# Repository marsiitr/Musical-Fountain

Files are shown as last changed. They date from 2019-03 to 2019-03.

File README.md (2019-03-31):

 # Musical-Fountain

 

## Abstract

 The idea behind the project is that we use the concept of nodes in sound, and use it to control the movement of servos and the brightness of LEDs.  

 We also added a stepper motor which rotates the entire revolute at a constant 30 steps per second. We also added another stepper motor which would control a central valve.

The nozzles were 3d printed to reduce the mannufacturing cost. For insulation, we mostly used locally available epoxy glue and araldite. 

## Motivation

From the outside , musical fountain seemed to be a trivial project. but, when we got into its technical aspects, it wasn't so. Everytime we came up with a design, we had to brainstorm it and eventually a new design came into picture.   
This challenge of coming up with an efficient model is what kept us motivated.

## Electronic Aspect  

1. An app named Audacity was used to export the data points corresponding to a song(the value of the data points signifies the voltage values of the sound signals).The extracted data was analyzed and plotted to see the maximum and minimum value of the data points.In the arduino code, the stepper was given a rotation after every 10 iterations and servo were rotated as per a fixed pattern of iterations.  
2. The Leds were made to dance as per the data points value by giving the range of value between the maximum and minimum values calculated before.For every specific command, functions were made and were called when required in the void loop.Also one more stepper motor was attached to a flow regulator to regulate the flow of water coming to the central nozzle.  
3. Dataset was made for 5 songs.As the space available in the arduino is limited , we used sd card to store the data points value and read the corresponding value in the code directly from the sd card.Most of the electronic parts like motors and wires were in the water, hence all the components were completely sealed and water proofed so that no damage is caused by water.

## Mechanical Aspect  
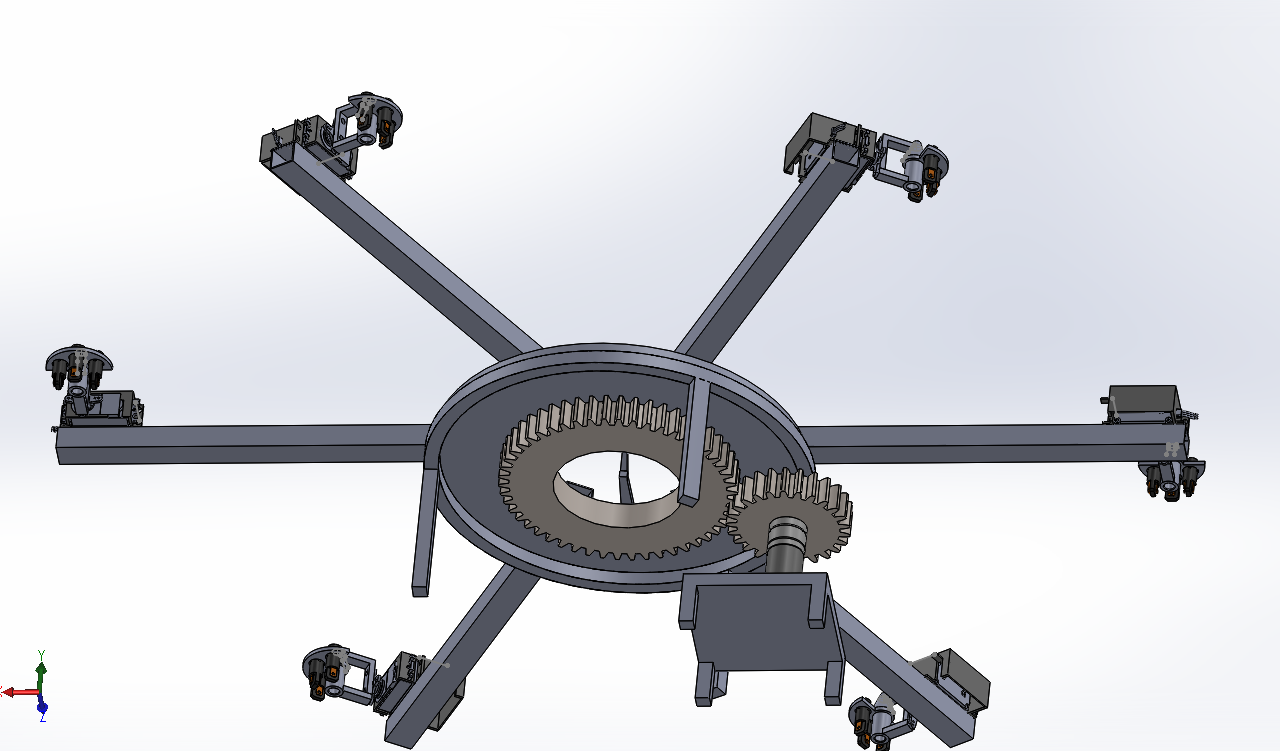
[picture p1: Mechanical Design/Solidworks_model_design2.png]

1. The revolute of the model was based on The Lazy Susan armature. we 3d printed the nozzles and 2 gears with 50 and 25 teeth respectively.  
2. 6 hollow tubes were attached on the lazy susan, at the end of each was a servo motor attached which would eventually control the movement of the nozzle.  
3. A secondary base was manufactured to setup the stepper motor which was used to rotate the armature. the secodary base also housed another stepper motor which would be controlling the valve. 3 pumps were used to pump water in the fountain.  

## Cost Structure  
|COMPONENTS | COST(₹)|
|----|---|
|Arduino Mega |  1300|
|Motor Drive |  160*2|
|Servo Motor |  325*6|
|Stepper | 690*2|
|Lazy Susan | 1250|
|Tub | 670|
|IC, BreadBoard, etc | 300|
|Wiring | 1000|
|LEDs | 350|
|M Seal, Araldite | 300|
|Aluminium Rod | 280|
|Central Valve | 300|
|Pump | 2000|
|Piping | 700 |
|Total Estimated Cost | 11,500|

## Application  

It has been observed that when soothing music is played near crops, there yeild increases. So this technique will be very helpful in drip irrigation. 
Also, musical fountain increases the aesthetic value of the place where it is established.  

## Limitation  

Our fountain's performance was greatly hindered by the pumps we used. Low quality piping and insulation can also be a contributing factor for bad performance.  
## Future Improvements  

We can improve the quality and way of insulation which was provided to the fountain's electrical components. Its base needed attention too. Also, pumps with higher values of Q should be used.  

## Team Members  

1. Archi Agarwal
2. Jalaj Madaan
3. Kshitij Srikant
4. Tabish Madni
5. Tejas Naik
6. Vaibhavi Chidella
7. Vipul Bansal  

## Mentors

1. Prachi Agarwal
2. Vandan Gajjar

## References  

1. https://ieeexplore.ieee.org/abstract/document/5230466
2. https://manual.audacityteam.org/man/tutorials.html
3. https://www.arduino.cc/en/Reference/SD
4. https://matplotlib.org/tutorials/introductory/pyplot.html
5. And some of the tips and ideas given by seniors :)

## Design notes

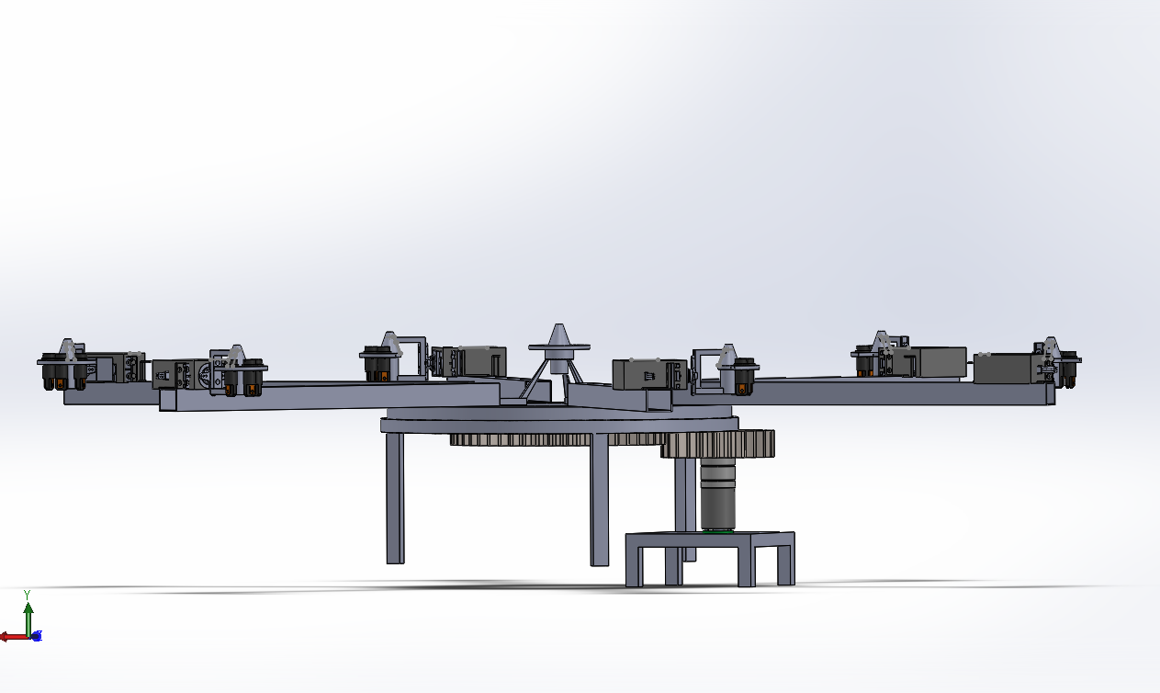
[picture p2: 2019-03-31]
Mechanical Design/Solidworks_model_design1.png

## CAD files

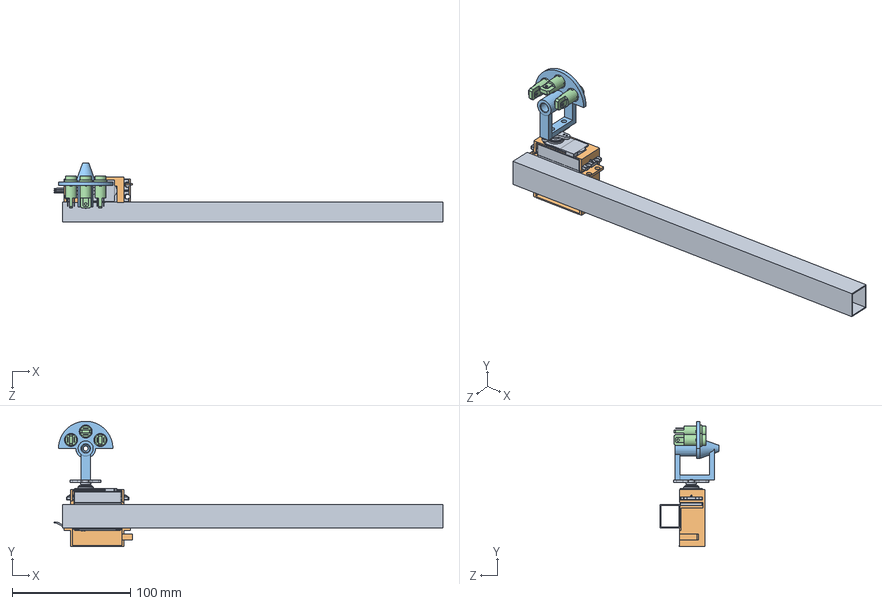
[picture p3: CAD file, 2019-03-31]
Mechanical Design/rod nossel.SLDASM
328.6 x 106.0 x 50.2 mm
rod
cover
sample 10
led x 3

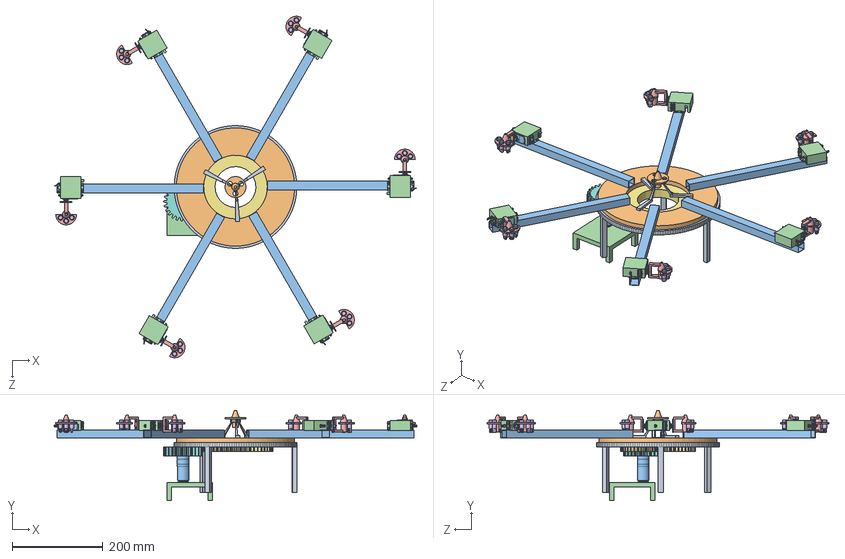
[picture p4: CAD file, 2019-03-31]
Mechanical Design/new musical fountain assembly.SLDASM
798.1 x 198.3 x 751.1 mm
lazy susan base
lazy susan representation
rod x 6
cover x 6
sample 10 x 6
led x 18
1 Inch - Spur gear 8DP 50T 14.5PA 0.787401575FW ---S50N3.0H2.0L0.03125N
Inch - Spur gear 8DP 25T 14.5PA 0.787401575FW ---S25N3.0H2.0L0.03125N
centre nossel base
centre nossel
Pololu-25D-12V-21kgcm-DCmotor
encoder base

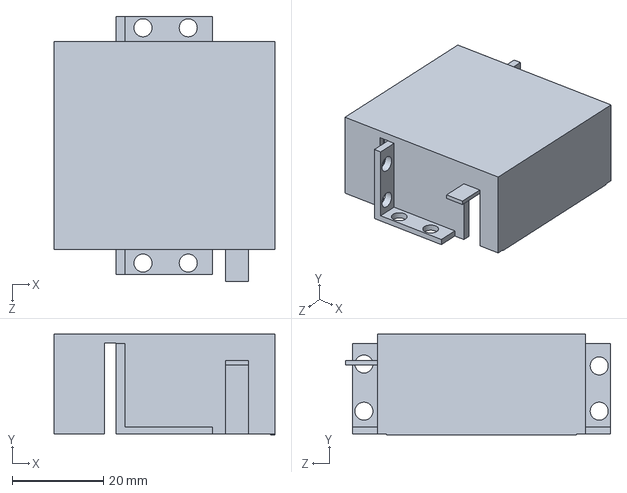
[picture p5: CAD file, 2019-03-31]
Mechanical Design/cover.SLDPRT
48.3 x 22.0 x 57.9 mm

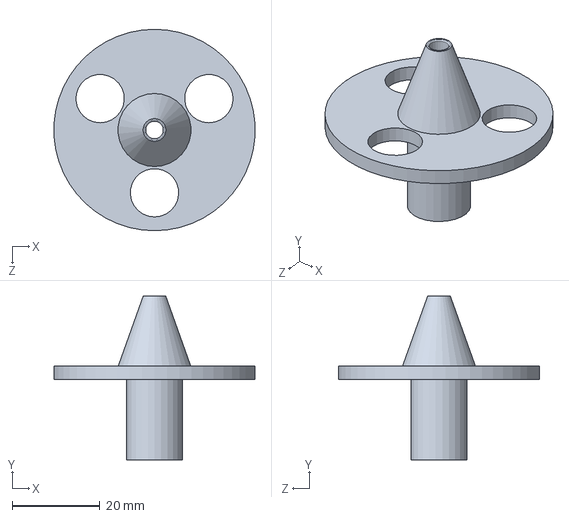
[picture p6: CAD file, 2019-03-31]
Mechanical Design/centre nossel.SLDPRT
45.9 x 37.4 x 46.0 mm

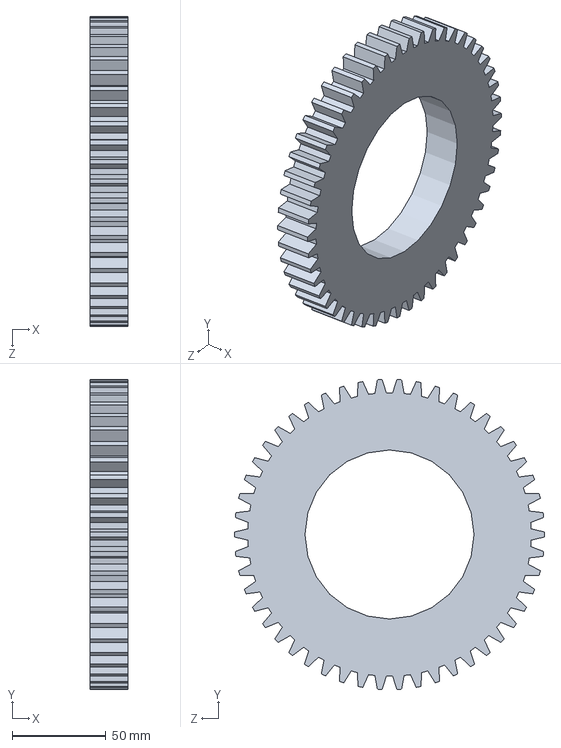
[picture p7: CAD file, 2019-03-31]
Mechanical Design/Gear Inch - Spur gear 8DP 50T 14.5PA 0.787401575FW ---S50N3.0H2.0L0.03125N.SLDPRT
20.0 x 164.9 x 165.1 mm

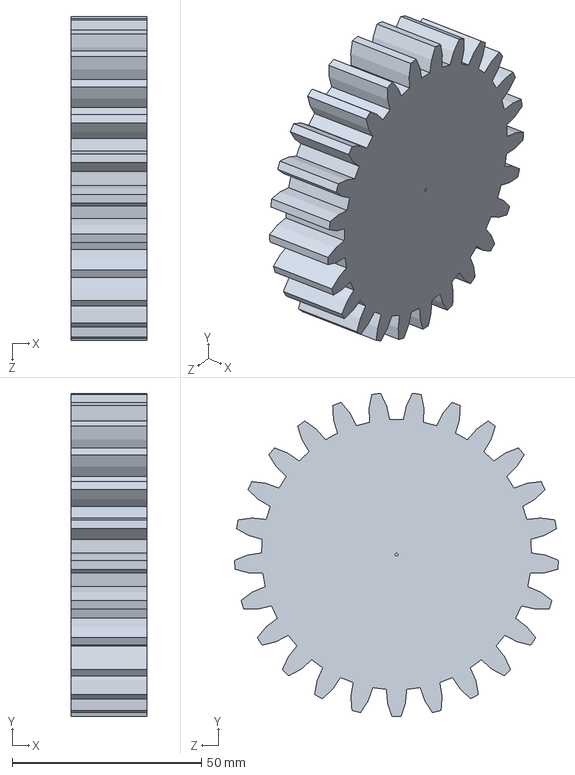
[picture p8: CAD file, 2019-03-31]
Mechanical Design/Inch - Spur gear 8DP 25T 14.5PA 0.787401575FW ---S25N3.0H2.0L0.03125N.sldprt
20.0 x 85.5 x 85.7 mm

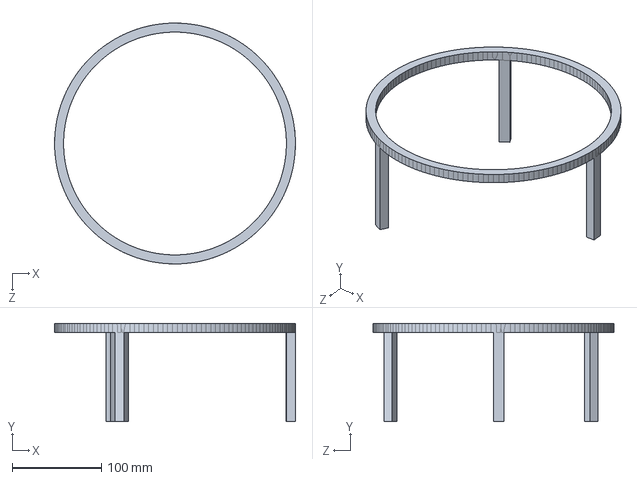
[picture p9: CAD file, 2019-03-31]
Mechanical Design/lazy susan base.SLDPRT
270.0 x 110.0 x 270.0 mm

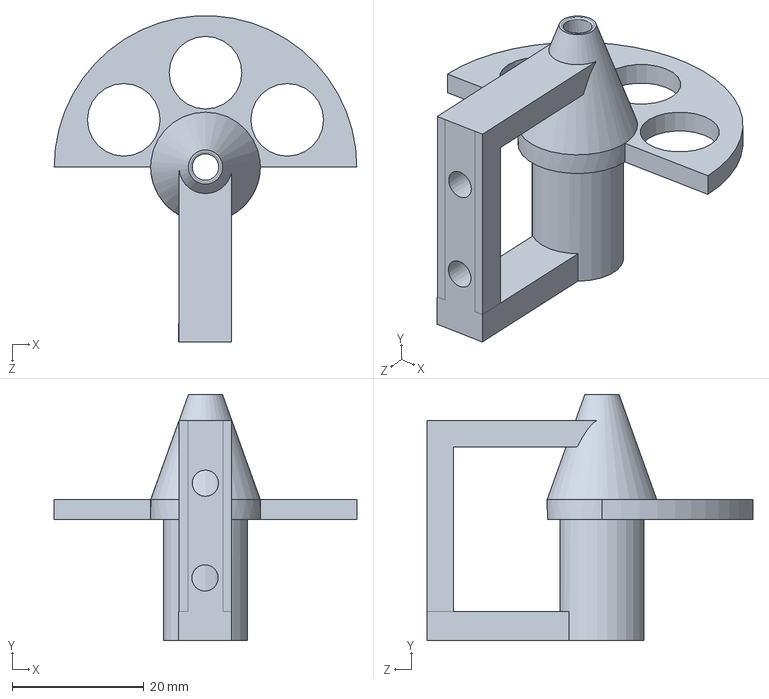
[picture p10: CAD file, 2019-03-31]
Mechanical Design/side nossel.SLDPRT
46.0 x 37.4 x 49.5 mm

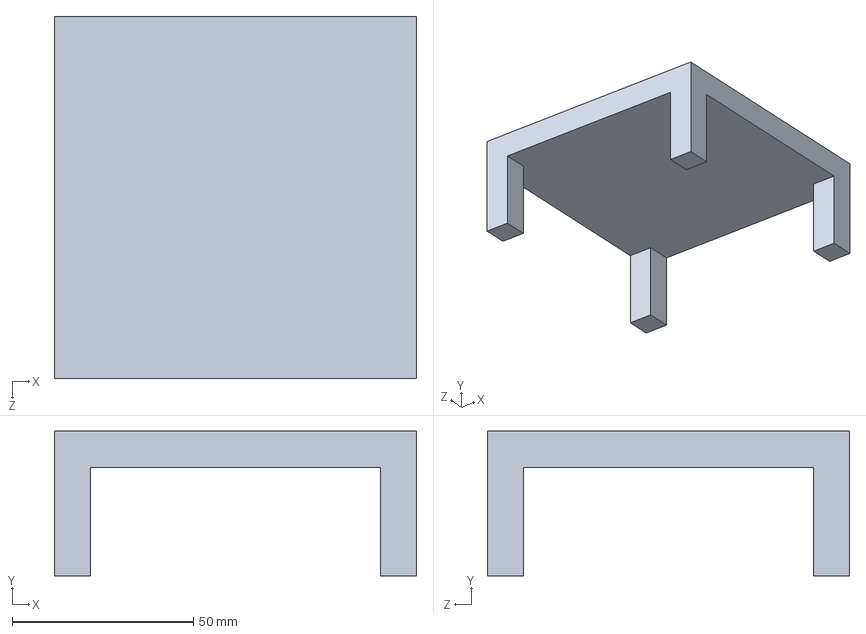
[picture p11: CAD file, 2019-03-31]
Mechanical Design/encoder base.SLDPRT
100.0 x 40.0 x 100.0 mm

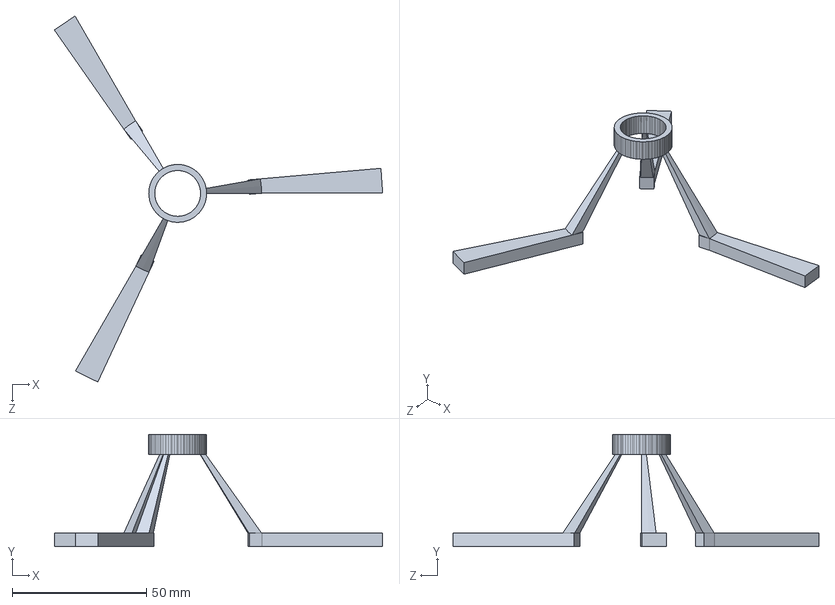
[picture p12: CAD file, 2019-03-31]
Mechanical Design/centre nossel base.SLDPRT
122.3 x 41.7 x 136.4 mm

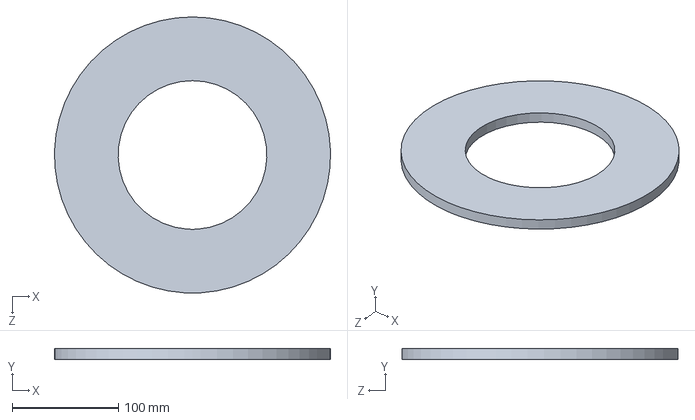
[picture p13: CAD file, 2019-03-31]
Mechanical Design/lazy susan representation.SLDPRT
259.9 x 10.0 x 260.0 mm

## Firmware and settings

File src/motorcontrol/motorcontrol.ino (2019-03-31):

#define s1 7           //defining servo pins on arduino
#define s2 8
#define s3 9
#define s4 10
#define s5 11
#define s6 12
#include <Servo.h>        //including servo library
#include <Stepper.h>      //including stepper library
int i =0;
int a1=200;            
int a2=20;

 int stepsPerRevolution = 200;                         // defining steps per Revolution for the stepper
Stepper myStepper(stepsPerRevolution, A0,A1,A2,A3);    //setting the stepper for gear revolution
Stepper myStepper1(stepsPerRevolution, 2,3,4,5);       //setting the stepper1 for controlling the flow regulator
Servo myservo1;                           //setting the servos                                                                                          
Servo myservo2;
Servo myservo3;
Servo myservo4;
Servo myservo5;
Servo myservo6;
void servoset()                 //function for setting the servo to 0 position

{myservo1.write(0);
myservo2.write(0);
myservo3.write(0);
myservo4.write(0);
myservo5.write(0);
myservo6.write(0);
  
}
void servomove(double x)         //function for the motion of servo to any angle x
{myservo1.write(x);
myservo2.write(x);
myservo3.write(x);
myservo4.write(x);
myservo5.write(x);
myservo6.write(x);
  
}
void motion() {                      //function for the motion of stepper
  // step one revolution  in one direction:
  Serial.println("clockwise");
  myStepper.step(a1);
a1=-a1;             //for making it revolve the other way
}
void motion2() {                    //function for the motion of stepper1
  myStepper1.step(a2);
  a2=-a2;
}
void setup() {
  // put your setup code here, to run once:
  Serial.begin(9600);

  myservo1.attach(s1);             //initializing the servos
myservo2.attach(s2);
myservo3.attach(s3);
myservo4.attach(s4);
myservo5.attach(s5);
myservo6.attach(s6);
 myStepper.setSpeed(30);          //setting the stepper speed
 myStepper1.setSpeed(10);         //setting the stepper1 speed

}

void loop() {
  // put your main code here, to run repeatedly:
  
  for (i=1;i<=9856;i++){                         //iterating over the number of data points obtained

  if(i%5==0 && i%30!=0 && i%20!=0 && i%10!=0)
 {
  servomove(25);
 }
 if (i%10==0 && i%30!=0 && i%20!=0){
servomove(0);
}
 if(i%20==0 && i%30!=0)
 {
  //motion();
  servomove(25);
  motion2();
  
 }
 if(i%30==0){
  servomove(0);
  motion();
  }
  }
 
  

}

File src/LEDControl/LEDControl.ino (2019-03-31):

#define oi 2        //defining pin for centre nozzle orange colour led
#define wi 3         //defining pin for centre nozzle white colour led
#define ri 5          //defining pin for centre nozzle red colour led
#define go 6           //defining pin for outer nozzles green colour led
#define wo 7            //defining pin for outer nozzles white colour led
#define ro 8             //defining pin for outer nozzles red colour led


#include <Servo.h>       //including servo library
#include <SD.h>          //including library for read from an sd card connected to arduino
#include <SPI.h>         //including library for connecting sd card to arduino
#include <Stepper.h>     //including stepper library
File myFile;

float readLineUser()
{
  String r;
  char c;
  while(myFile.available())
  {
    c=myFile.read();
    if(c==',')
    {
      return (r.toFloat());
    }
    else if(c=='\n')
    {
      r="";
      
    }
    else
    {
      r+=c;
    }
  }
}

//below are the functions for glowing and turning off different leds in pairs
void ored()
{
  digitalWrite(oi,HIGH);
  digitalWrite(ro,HIGH);
}
void ogreen()
{
  digitalWrite(oi,HIGH);
  digitalWrite(go,HIGH);
}
void owhite()
{
  digitalWrite(oi,HIGH);
  digitalWrite(wo,HIGH);
}
void wred()
{
  digitalWrite(wi,HIGH);
  digitalWrite(ro,HIGH);
}
void wgreen()
{
  digitalWrite(wi,HIGH);
  digitalWrite(go,HIGH);
}
void rgreen()
{
  digitalWrite(ri,HIGH);
  digitalWrite(go,HIGH);
}
void rwhite()
{
  digitalWrite(ri,HIGH);
  digitalWrite(wo,HIGH);
}
void multi()
{
  digitalWrite(oi,HIGH);
  digitalWrite(wi,HIGH);
  digitalWrite(ri,HIGH);
  digitalWrite(wo,HIGH);
  digitalWrite(ro,HIGH);
  digitalWrite(go,HIGH);
}
void low()
{
  digitalWrite(oi,LOW);
  digitalWrite(wi,LOW);
  digitalWrite(ri,LOW);
  digitalWrite(wo,LOW);
  digitalWrite(ro,LOW);
  digitalWrite(go,LOW);
}


void setup() {

 
  
pinMode(oi,OUTPUT);
pinMode(wi,OUTPUT);
pinMode(ri,OUTPUT);
pinMode(go,OUTPUT);
pinMode(wo,OUTPUT);
pinMode(ro,OUTPUT);
 // Open serial communications and wait for port to open:
  Serial.begin(9600);
  while (!Serial) {
    ; // wait for serial port to connect. Needed for native USB port only
  }


  Serial.print("Initializing SD card...");

  if (!SD.begin(4)) {
    Serial.println("initialization failed!");
    while (1);
  }
  Serial.println("initialization done.");
 myFile = SD.open("SongData.txt");
  // open the file. note that only one file can be open at a time,
  // so you have to close this one before opening another.
}
void loop() {
   myFile = SD.open("SongData.txt");
  while(myFile.available()) {
    double s=readLineUser();                     //storing the data point value in a variable s
    low();
    
if ((s>0)&&(s<=5)){
 multi();
 }
 if ((s>5)&&(s<=10)){
  ored();
 }
if ((s>10)&&(s<=15)){
  ogreen();
 }  
if ((s>15)&&(s<=20)){
  owhite();
 }
if ((s>920)&&(s<=25)){
wred();
 }
 if ((s>25)&&(s<=30)){
 wgreen();
 }
 if ((s>30)&&(s<=35)){
  rgreen();
 }
 if ((s>35)){
 rwhite();
 }
 

 delay(107.54);
 
}
  
myFile.close();
}

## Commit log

2019-03-31 changes done
    [Gear Inch - Spur gear 8DP 50T 14.5PA 0.787401575FW ---S50N3.0H2.0L0.03125N.SLDPRT, Inch - Spur gear 8DP 25T 14.5PA 0.787401575FW ---S25N3.0H2.0L0.03125N.sldprt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]
2019-03-31 Created new folder A
    [Gear Inch - Spur gear 8DP 50T 14.5PA 0.787401575FW ---S50N3.0H2.0L0.03125N.SLDPRT, Inch - Spur gear 8DP 25T 14.5PA 0.787401575FW ---S25N3.0H2.0L0.03125N.sldprt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]
2019-03-31 deleted mech design
    [Gear Inch - Spur gear 8DP 50T 14.5PA 0.787401575FW ---S50N3.0H2.0L0.03125N.SLDPRT, Inch - Spur gear 8DP 25T 14.5PA 0.787401575FW ---S25N3.0H2.0L0.03125N.sldprt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]
2019-03-31 renamed A
    [Gear Inch - Spur gear 8DP 50T 14.5PA 0.787401575FW ---S50N3.0H2.0L0.03125N.SLDPRT, Inch - Spur gear 8DP 25T 14.5PA 0.787401575FW ---S25N3.0H2.0L0.03125N.sldprt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]
